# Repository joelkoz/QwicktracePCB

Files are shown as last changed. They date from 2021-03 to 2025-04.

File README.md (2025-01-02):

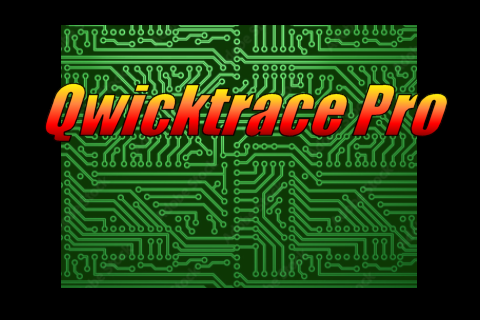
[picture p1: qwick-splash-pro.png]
Qwicktrace Logo


# Qwicktrace Pro PCB
Qwicktrace PCB is the software component of the QwickFab PCB open source desktop circuit board fabrication system.
The system dramatically reduces the time and skill required to make top quality single and double sided circuit 
boards for prototyping and one off use. Using QwickFab PCB, making a PCB is as simple as uploading your Gerber files to 
the Pro controller, selecting the process you wish to use to create the board, and then following the on-screen step
by step instructions. 

# Overview
The QwickFab desktop fabrication system consists of three major hardware components and one optional one:
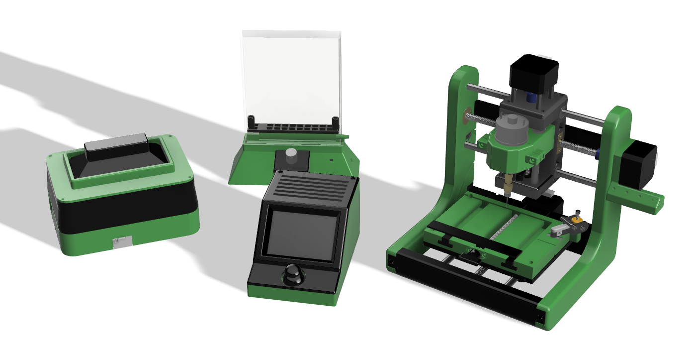
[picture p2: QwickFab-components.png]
Qwicktrace components


1. The Qwicktrace Pro Controller is small control device with touchscreen and joystick powered by a Raspberry Pi 4 and the software
found in this repository. It is comprised of a software stack and UI for controlling the other two hardware components below. The 
Controller can run either of the two other components individually, or together as a complete desktop PCB fabrication system.

2. The Qwicktrace Exposure Table is a small device for quickly exposing photosensitive copper boards to ultraviolet light masked using a process called "Masked Stereolithography" (MSLA). The all new design of this exposure system adds an amber LED "safe light" for illuminating the mask for end user board positioning that is invisible to the photosenstive board.

3. The Qwickmill mini CNC is a small desktop CNC machine designed specifically for working with small printed circuit boards. It can
quickly drill the holes needed by through hole components on boards processed with the Exposure table.  It can also mill an entire PCB on blank copper boards using special ingraving bits. This is handy if your board is simple enough as to not need the better resolution of the exposure table, or if you are on a budget and would prefer not to spend the extra money on photosensitive boards. 
Finally, the Qwickmill can be used to cut board stock down to smaller sizes.

4. The QwickEtch Etching tank is a small container that can be used to quickly etch boards exposed with the Exposure table using
a minimal mount of equipment. While any type of container can be used, the QwickEtch tank has an air pump powered agitator in
in, removing the need for you to manually rock the etching tank.

The software on the Pro Controller (source code found on this repo) handles the more challenging aspects of making a PCB, such as aligning the drilling with the traces made on the exposure table, or positioning the opposite side of a board on a double sided PCB.

While the above hardware components make for a convenient set of tools, many Makers already have existing equipment they'd like
to use in place of a QwickFab component. You are free to mix and match any or all of the components that you wish.  You could
in theory build NONE of the hardware components and simply run the Qwicktrace software on an old laptop or pre-existing 
Raspberry Pi build.  The Qwickmill is built upon the open source standard Grbl controller. If you already own a CNC machines that uses Grbl, you can use that instead. It is easy to create a cable that connects from the Pro Controller to any CNC machine, such a 3018 or 1610. If you are on a budget, you can sometimes source a kit for one of these machines for less money than the individual parts for building the Qwickmill.

# Software features

* Creates PCB trace masks directly from Gerber files in SVG for MSLA exposure and/or in g-code for isolation milling
* Software deskewing of traces and drill holes makes combining MSLA, milling, and/or double sided boards quick and easy.
* Software autoleveling ensures isolation milling traces are cut to perfect depth
* Drill/mill features works with any Grbl compatible CNC controller
* UI designed for small 3.5" touchscreen
* Supports joystick input via ADS1115 for easy jogging of CNC machine and alignment of drill holes
* Turns Raspberry Pi into a remote access server and controller for Grbl CNC machines

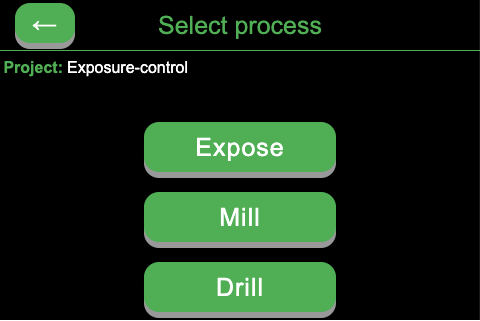
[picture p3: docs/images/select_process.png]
Select process

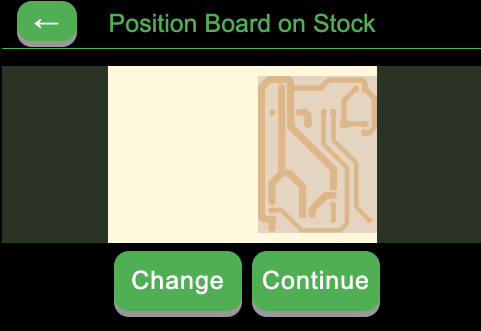
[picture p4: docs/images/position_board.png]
Position board


# DIY construction of a QwickFab system
Qwicktrace components

The Qwickfab Pro system is made from parts printed with your 3D printer as well as easy to obtain off the shelf parts. The
STL files for this project can be found here in this repo in the `hardware/*/stl` directories. A complete bill of materials can be
found in the `docs` directory.

Build instructions with project discussion is located on the project's [Hackaday Project Page](https://hackaday.io/project/182645-qwickfab-pcb)

To install the software on the Raspberry Pi, see the file `Setting up Raspberry Pi`, also in `docs`

# Development

The Qwicktrace user interface on the Pro Controller is a touchscreen app written in NodeJS/Javascript and built with the
Electron framework.  This UI is layered on top of a software stack comprised of many great open source software packages. These include:

1. [Tracespace](https://github.com/tracespace) Gerber processing library for Javascript
2. [pcb2gcode](https://github.com/pcb2gcode/pcb2gcode) Gerber to GCode utility for milling isolation traces
3. [CNCjs](https://github.com/cncjs/cncjs) Web interface and Grbl server for CNC machine control
4. [EventEmitter2](https://github.com/EventEmitter2/EventEmitter2) Advanced event handling for NodeJS

For additional technical information on the Qwicktrace software architecture, see the `docs` directory

---
### Do you find my work useful?

<a href="https://www.buymeacoffee.com/joelkoz" target="_blank">Buy Me A Coffee</a>
---

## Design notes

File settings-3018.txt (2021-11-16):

$0=10 (Step pulse time, microseconds)
$1=25 (Step idle delay, milliseconds)
$2=0 (Step pulse invert, mask)
$3=6 (Step direction invert, mask)
$4=0 (Invert step enable pin, boolean)
$5=0 (Invert limit pins, boolean)
$6=0 (Invert probe pin, boolean)
$10=1 (Status report options, mask)
$11=0.020 (Junction deviation, millimeters)
$12=0.002 (Arc tolerance, millimeters)
$13=0 (Report in inches, boolean)
$20=0 (Soft limits enable, boolean)
$21=1 (Hard limits enable, boolean)
$22=1 (Homing cycle enable, boolean)
$23=0 (Homing direction invert, mask)
$24=25.000 (Homing locate feed rate, mm/min)
$25=1000.000 (Homing search seek rate, mm/min)
$26=250 (Homing switch debounce delay, milliseconds)
$27=1.000 (Homing switch pull-off distance, millimeters)
$30=20000 (Maximum spindle speed, RPM)
$31=0 (Minimum spindle speed, RPM)
$32=0 (Laser-mode enable, boolean)
$100=800.000 (X-axis travel resolution, step/mm)
$101=800.000 (Y-axis travel resolution, step/mm)
$102=800.000 (Z-axis travel resolution, step/mm)
$110=1000.000 (X-axis maximum rate, mm/min)
$111=1000.000 (Y-axis maximum rate, mm/min)
$112=600.000 (Z-axis maximum rate, mm/min)
$120=50.000 (X-axis acceleration, mm/sec^2)
$121=50.000 (Y-axis acceleration, mm/sec^2)
$122=50.000 (Z-axis acceleration, mm/sec^2)
$130=289.000 (X-axis maximum travel, millimeters)
$131=175.000 (Y-axis maximum travel, millimeters)
$132=37.85 (Z-axis maximum travel, millimeters)

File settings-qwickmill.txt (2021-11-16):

$0=10 (Step pulse time, microseconds)
$1=25 (Step idle delay, milliseconds)
$2=0 (Step pulse invert, mask)
$3=2 (Step direction invert, mask)
$4=0 (Invert step enable pin, boolean)
$5=0 (Invert limit pins, boolean)
$6=0 (Invert probe pin, boolean)
$10=1 (Status report options, mask)
$11=0.010 (Junction deviation, millimeters)
$12=0.002 (Arc tolerance, millimeters)
$13=0 (Report in inches, boolean)
$20=0 (Soft limits enable, boolean)
$21=1 (Hard limits enable, boolean)
$22=1 (Homing cycle enable, boolean)
$23=0 (Homing direction invert, mask)
$24=25.000 (Homing locate feed rate, mm/min)
$25=1000.000 (Homing search seek rate, mm/min)
$26=250 (Homing switch debounce delay, milliseconds)
$27=1.000 (Homing switch pull-off distance, millimeters)
$30=26666 (Maximum spindle speed, RPM)
$31=0 (Minimum spindle speed, RPM)
$32=0 (Laser-mode enable, boolean)
$100=400.000 (X-axis travel resolution, step/mm)
$101=400.000 (Y-axis travel resolution, step/mm)
$102=400.000 (Z-axis travel resolution, step/mm)
$110=1000.000 (X-axis maximum rate, mm/min)
$111=1000.000 (Y-axis maximum rate, mm/min)
$112=600.000 (Z-axis maximum rate, mm/min)
$120=30.000 (X-axis acceleration, mm/sec^2)
$121=30.000 (Y-axis acceleration, mm/sec^2)
$122=30.000 (Z-axis acceleration, mm/sec^2)
$130=200.000 (X-axis maximum travel, millimeters)
$131=200.000 (Y-axis maximum travel, millimeters)
$132=200.000 (Z-axis maximum travel, millimeters)

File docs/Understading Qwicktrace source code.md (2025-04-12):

General functionality of QwicktracePCB app:
========

Workflow
------
- User creates a collection of Gerber files for each layer of a PCB, and a DRL file for hole definitions using
  their EDA (KiCad, Eagle, etc.). 
  - Be sure that the origin of your board is at the lower left hand corner
  - Files that represent the top and/or bottom copper layer, along with the DRL file should be bundled into a single .zip file.
  - The .ZIP file name is used as the project name inside of QwicktracePCB. 
  - The .ZIP file name should NOT contain any spaces
- Upload the .ZIP file to the app using `http://pcb.local:8080`
- Use the UI of QwicetracePCB to fabricate the board

Troubleshooting
-------
- Just before milling or exposure starts, the gerber and drill files actually used will be stored in `/temp`
- You can examine the .GBR or .DRL files with the `gerbv` utility to make sure they represent your board.
- Gcode used for milling and drilling are stored in `/temp` with file extensions `.nc`
- You can manually updload the `.nc` files and manually control the milling process by accessing CNCjs directly
  at `http://pcb.local:8000`
- Since the CNC mill is controlled via the CNCjs layer, you can actually run the QuicktracePCB UI and control code directly 
  from a PC or Mac and observe the logs.
  - Edit the `config.json` file and change the `cnc.server.host` and the `pigpio.host` entries to be the IP of
    the Qwicktrace controller. Do NOT use the DNS name "pcb.local", as the code may not properly resolve those names
  - Run the Qwicktrace UI from the desktop by changing the current directory to the `QwicktracePCB` root and
    executing `npm run start` from the terminal.

- Regenerate gcode for traces with
```
pcb2gcode --front ./temp/mirror-bottom.gbr --front-output ./temp/bottom-mill.nc
```

Project outline
-----
- Source code is in `app` directory
- ZIP files of gerber/drill bunders are stored in `pcb-files`
- Definitions for raw material types and stock of those materials are in `profiles`
  - A "material" defines a general type of raw material (copper board, photosenstive board, etc)
  - A "stock" is a raw material cut to a particular size
- Configuration file for app is `config.json`. It defines the fabrication tools available and their configuration
  - use `config-3018.json` if milling pcb with a standard 3018 CNC Mill
  - use `config-pi-pro.json` if milling and/or exposing with a Qwickpro build
- If pcb trace isolation is done using a mill, then `pcb2gcode` app is used to translate gerber into gcode. The
  file `millproject` defines the parameters passed in to this CLI app. 

Source overview
------
- App is a desktop app that uses Electron to provide a runtime environment
- App is structured as a typical client/server app, even though it is bundled inside Electron
- "Server" code is the only code that can talk to/control hardware (hard drive, mill, exposure table)
- "Client" code is a html+javascript web app
- "Server" code is located in `main` directory
- "Client" code is located in `render` directory
- The two layers communicate with each other with a publish/subscribe model using message queue management provided
  by `MainMQ.js` and `RenderMQ.js`
- There is a "remote procedure call" mechanism built on top of `MainMQ.js` and `RenderMQ.js` named `RPCServer.js` and 
  `RPCClient.js` respectively
- The main application logic and program flow is handled in the "Client".  The "Server" provides supporting services
  and does the actual work.

Server side code
------------
- Code found in `app/main`
- `main.js` is the server side entrypoint with startup code. It creates the Electron browser window for the UI,
   loads the UI (via `UILoader.js`), then sets up message handers the client may call
- `ProjectLoader.js` is a singleton that manages a collection of all of the PCB projects stored in `pcb-files.js`
  - Each entry is an instance of `pcb/PCBProject.js`
  - Each project is sent to the UI for user selection
  - Has a method named `prepareForWork()` that prepares all of the files necessary to be processed
- `ProfileLoader.js` is a singleton that reads the definitions of all of the material and stock profiles and sends
   them to the ui
- A series of "Controller" objects control the various hardware sub systems. Each are a collection of work methods
  that do the work of fabrication.  Many can be called directly by the client via the RPC mechanism (look for 
  `this.rpcAPI()` to see what methods are exposed as callable via RPC).
  - `CNCController.js` handles milling and drilling
  - `JoystickController.js` handles the system joystick
  - `UVController.js` handles the exposure table
- A low level CNC control object that interfaces with CNCjs can be found in `cnc/CNC.js`
- If milling a PCB's traces using trace isolation, Gerber to GCode translation is handled by the `pcb2gcode`
  command line tool. `cnc/GcodeUtils.js` is the server's interface to this tool which invokes `pcb2gcode`

Client side code
----------------
- Code found in `app/render`
- UI is composed of a series of individual "pages" that the user moves through.
  - Pages are located in `app/render/ui`
  - A page definition contains CSS and a root `&lt;DIV&gt;`. The `DIV` in turn can contain
    whatever HTML needs to be displayed
  - Page flow is controlled by `UIController.js`
  - A "wizard" is a collection of pages that leads a user step by step thru a particular
    function. Wizards are created by definition a JSON structure that contains the name
    of the wizard and a series of "steps". Each step composed of a string id that identifies the
    step, text instructions to give the user, the buttons to present to the user and the "handler"
    code to execute when that button is pressed, as well as code to execute then the page is first
    activated, and when it is deactivated.
- A series of "Controller" objects represent by each functional subsystem. They define both the
  UI of that subsystem, as well as handle the communication with the hardware controllers on the "server"
  via RPC. Generally, a feature will define a wizard to handle the feature, then will delegate to the
  UIController to execute the wizard.
  - `UIController.js` Top level UI that delegates to the various features and sub-systems. Also executes
     the "wizard" UI feature.
  - `DrillController.js` Feature allows thru holes to be drilled in a PCB
  - `MillController.js` Feature that allows a PCB to be fabricated using a CNC to do trace isolation
  - `ExposeController.js` Featuure that allows a PCB to be fabtricated using UV sensitive PCB boards
  - `PositionController.js` A sub-system that allows the user to position the traces on stock of a particular size
  - `SettingsController.js` Feature allows user to modify system configuration, as well as perform utility functions
    like cutting stock

PCB milling
=====================
- Gerber and DRL files are converted to GCode for milling by:
- `app/main/ProjectLoader.js` methods `prepareForWork()`, `getFinalGerber()`, and `getWorkAsGcode()`
- `prepareForWork()` and `getFinalGerber()` takes the project files and transforms them, positioning
  them on the stock, and mirroring the traces (if milling the bottom of the board). Transformed
  gerber files are placed in the `/temp` directory
- `getWorkAsGcode()` translates those files in Gcode via `app/main/cnc/GcodeUtils.js`, and stores the
  results in the `/temp` dir as `.nc` files.
- `GcodeUtils.js` delegates to `pcb2gcode` to do the actual translation, Parameters to `pcb2code` are stored
  in the `millproject` file.  
- To actually mill the traces of a PCB, `app/render/MillController.js` makes the rpc call `cnc.millPCB` which
  is executed by `app/main/CNCController.js` in the `millPCB()` method. That in turn makes a series of calls
  to `app/cnc/CNC.js` to control each step of the milling process.

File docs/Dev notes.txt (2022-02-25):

RaspPi splash screen is here
/usr/share/plymouth/themes/pix/splash.png

Thus, plymouth is already installed.

Ideas:
Use input pin to specify if probe arm is connected or not.  Use status report from grbl to see if 
clip is connected or not.  Thus:
1. Ground clip screw
2. Connect pin from pi to arm strip and read to see if arm is in place

Remove M3 from pcb2gcode output, and use our own ramp up code to turn on spindle.

Add a red "emergency stop" button to bit holder and connect it to Grbl alarm pin

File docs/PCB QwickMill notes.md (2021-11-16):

# Qwicktrace PCB Pro Notes

This file contains general notes I made as I was developing the mill and its software.

## Tips and tricks for milling

### Critical tips
* Bit must be TIGHT. Otherwise, vibration causes slip, which ruins z-height.
* X and Y bearings must be secure. Y bearing slipped out, ruining z-height during mill

### Important tips
* When cutting, there is some wobble in the bit, so make sure to give a little extra room when 
  locating position
* 1mm drill bit is fairly large.  0.9mm is better. 0.8mm is tight fit, but some components may not fit
* 30 degree VBit made a much smoother cut than then 5/32" end mill

### Helpful hints
* Place a sheet of tin foil over milled PCB to be able to zprobe or autolevel it
* Scouring pad is great to clean up loose copper bits after milling

## Controller display
Connect hdmi cable for the Sharp display used in the exposure table to HDMI:0

External Display (i.e. any local display) would be HDMI:1

Customizing splash screen:
https://shop.sb-components.co.uk/blogs/posts/customising-splash-screen-on-your-raspberry-pi

## Important GCodes
```
G21 = Units in mm
G0 = Rapid position
G1 = Linear interpolation (position at current feedrate defined by previous "F")
```

Spindle on:
```
M03 S20000.0
```

Spindle off:
```
M05
```
```
G91 = Relative coordinate mode
G90 = Absolute coordinate mode
```
Doing a single probe (feed 20mm per minute, up to 14mm down from current point):
```
G91
G38.2 Z-14 F20
G90
```

## Using gerbv 

gerbv in GUI mode (just issue gerbv) allows one to examine gerber files
and drill files visually (e.g. look at intermediate files)

Using gerbv to manipulate gerber files:
```
// Rotate gerber clockwise 90 degrees:
gerbv -u mm -x rs274x -T "0x${width}r270" -o "${outFile}" "${inFile}"
```

```
// Rotate gerber counter clockwise 90 degrees:
gerbv -u mm -x rs274x -T "${height}x0r90" -o "${outFile}" "${inFile}"
```

## Using pcb2gcode to generate gcode for mill:

Create a file named "millproject" to save parameters
(vs. issuing on cli):
```
## Default options passed to pcb2gcode when generating
metric=true
metricoutput=true

# For use with grbl
software=custom
nog64=true
nog81=true

# Engraving traces
zwork=-0.25
zsafe=5
mill-feed=40
mill-speed=8500
offset=0.5

# Drilling holes
zdrill=-2.1
zchange=1.0
drill-feed=75
drill-speed=6000
onedrill=true
```
Since we manipulate gerber files internally (e.g. bottom files are
mirrored then saved to intermediate gerber file), always specify
"front" for pcb2gcode so it won't mirror a second time.

Generate gcode for copper:
```
pcb2gcode --front inputFileName.gbr --front-output outputFileName.nc
```

Generate gcode for drilling:
```
pcb2gcode --drill-side front --drill inputFileName.drl --drill-output outputFileName.nc
```

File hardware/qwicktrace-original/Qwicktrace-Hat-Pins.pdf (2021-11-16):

VCC + LED | 3.3v | 1 | 2 | 5v
I2C SDA | GPIO 2/SDA | 2 | 4 | 5v
I2C SCL | GPIO 3/SCL | 5 | 6 | GND
| GPIO 4 (GPCLK0) | 7 | 8 | GPIO 14 (TX) | UV LED BED
| GND | 9 | 10 | GPIO 15 (RX)
CS | GPIO 17 | 11 | 12 | GPIO 18 (PCM_CLK)
RESET | GPIO27 | 13 | 14 | GND
DC | GPIO 22 | 15 | 16 | GPIO 23
| 3.3v | 17 | 18 | GPIO 24
MOSI + T_DIN | GPIO 10 (MOSI) | 19 | 20 | GND
MISO + T_DO | GPIO 9 (MISO) | 21 | 22 | GPIO 25
SCK + T_CLK | GPIO 11 (SCLK) | 23 | 24 | GPIO 8 (CE0)
| GND | 25 | 26 | GPIO 7 (CE1)
| GPIO 0 (ID_SD) | 27 | 28 | GPIO 1 (ID_SC)
T_CS | GPIO 5 | 29 | 30 | GND
T_IRQ | GPIO 6 | 31 | 32 | GPIO 12 (PWM0)
| GPIO 13 (PWM1) | 33 | 34 | GND
CNC ZProbe | GPIO 19 (PCM_FS) | 35 | 36 | GPIO 16 | BUZZER
CNC LASER PTR | GPIO 26 | 37 | 38 | GPIO 20 (PCM_DIN)
GND | GND | 39 | 40 | GPIO 21 (PCM_DOUT)

1

Pi Hat to TFT wiring

16 Ribbon wire color | Multi/Shared 40 Pin | GPIO num | 40 Pin Num | 40 pin Col 1 row num | IDC 16P pin number | TFT connection | Make Longer
Brown | * | 3v3 | 1 | 1 | 1 | VCC
Red | * | 3v3 | 1 | 1 | 2 | LED | **
Orange | | GND | 9 | 5 | 3 | GND
Yellow | | GPIO17 | 11 | 6 | 4 | CS
Green | | Unused | | | 5
Blue | | GPIO27 | 13 | 7 | 6 | DC
Purple | | Unused | | | 7
Grey | | GPIO22 | 15 | 8 | 8 | RESET
White | * | MOSI/GPIO10 | 19 | 10 | 9 | T_DIN | **
Black | * | MOSI/GPIO10 | 19 | 10 | 10 | SDI(MOSI)
Brown | * | MISO/GPIO9 | 21 | 11 | 11 | SDO(MISO)
Red | * | MISO/GPIO9 | 21 | 11 | 12 | T_DO
Orange | * | SLCK/GPIO11 | 23 | 12 | 13 | SCK
Yellow | * | SLCK/GPIO11 | 23 | 12 | 14 | T_CLK
Green | | GPIO6 | 31 | 16 | 15 | T_CS
Blue | | GPIO5 | 29 | 15 | 16 | T_IRQ

1

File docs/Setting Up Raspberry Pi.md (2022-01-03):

# Setting up Raspberry Pi
This is a very rough list of things needed to do to setup the Raspberry Pi and install this QwicktracePCB controller software on it

1. Download and use "Raspberry Pi Imager" to flash an SD card from your desktop computer. Use recommended 32 bit OS on main menu. You need the OS 'with Desktop Software'.

2. Before installing the SD card in the Pi, create the file `ssh` in the root directory of the SD card. This can be done on a Mac by using Terminal, then typing `echo >/Volumes/boot/ssh`

3. On the same SD card, create the file `wpa_supplicant.conf` with the following contents:
```
country=US
ctrl_interface=DIR=/var/run/wpa_supplicant GROUP=netdev
update_config=1

network={
  ssid="NETWORK-NAME"
  psk="NETWORK-PASSWORD"
}
```

4. Replace the contents of the file `config.txt` on the SD card with the file found in the `pi-config/boot` directory of this project. It can be downloaded to your desktop computer using [this link](https://raw.githubusercontent.com/joelkoz/QwicktracePCB/main/pi-config/boot/config.txt).

5. Put the SD card in the Pi and boot. 

6. Use `ssh` to connect to the Pi from your desktop. It should be available on your network as `raspberrypi.local`.  Thus, `ssh pi@raspberrypi.local` should connect you. The default password is `raspberry`.

7. Change the password using the `passwd` command.

8. Install the software for whichever screen you are using. For the new "Qwicktrace Pro" controller, follow
the directions found in the `U6111-UC640.pdf` file in the `docs` directory of this repo.

8. Update all software using these commands:
```
sudo apt update
sudo apt full-upgrade
```

9. Configure the system with raspi-config:
```
sudo raspi-config

   *  Use the System Options to specify "Boot to command line" (in case something weird goes wrong)
   
   *  Change the host name to `pcb`
```

10. Install required software and utilities:
```
sudo apt-get update
sudo apt-get install nodejs
sudo apt-get install npm
sudo apt-get install fbi
```

11. From your home Pi directory, install the software from this project:
```
cd ~
git clone https://github.com/joelkoz/QwicktracePCB
cd QwicktracePCB
npm install
```

12. Install the X11 multihead configuration:
```
sudo cp /home/pi/QwicktracePCB/pi-config/x11/99-multihead.conf /usr/share/X11/xorg.conf.d
```

13. Enable the `pigpiod` daemon to give the software access to the GPIO pins:
```
sudo nano /lib/systemd/system/pigpiod.service
change line to:
ExecStart=/usr/bin/pigpiod -n 127.0.0.1 -p 8888

save file

sudo systemctl daemon-reload
sudo systemctl enable pigpiod
sudo service pigpiod start
```

NOTE: If you want to be able to access pigpiod remotely (for remote development, for example),
add additional allowed IP addresses to the `ExecStart` command above:
```
ExecStart=/usr/bin/pigpiod -n 127.0.0.1 -n 192.168.0.152 -p 8888
```

15. Disable Bluetooth related services:
```
sudo systemctl disable hciuart.service
sudo systemctl disable bluetooth.service
```

15. Disable other unneeded services
```
sudo systemctl disable cups.service cups.socket cups.path
sudo systemctl disable cups-browsed.service
```

15. Reboot the Pi:
```
sudo reboot
```

16. Connect back to the Pi via ssh. The DNS name of the machine should now be `pcb.local`, so use `ssh pi@pcb.local`

17. Test to see if the small SPI screen is working. An image on the small screen should appear after:
```
sudo fbi -T 7 -d /dev/fb2 -noverbose /home/pi/QwicktracePCB/qwick-splash-pro.png
```

18. Configure desktop to run Qwicktrace exclusively:
```
sudo cp /etc/xdg/lxsession/LXDE-pi/autostart /etc/xdg/lxsession/LXDE-pi/autostart-desktop

sudo cp /home/pi/QwicktracePCB/pi-config/lxde/autostart-app /etc/xdg/lxsession/LXDE-pi

sudo cp /etc/xdg/lxsession/LXDE-pi/autostart-app /etc/xdg/lxsession/LXDE-pi/autostart
```

19. Disable cursor on touchscreen:
```
sudo nano /etc/lightdm/lightdm.conf

Find the [Seat*] section, uncomment the "#server-command=" line, and make it:

xserver-command=X -nocursor
```

20. Install the splashscreen services
```
sudo cp /home/pi/QwicktracePCB/pi-config/etc/systemd/system/* /etc/systemd/system
sudo systemctl enable splashscreen.service
```

20. Install CNC control services (if using QwickMill or other CNC machine):
The following steps come from the official [CNCjs Pi install pages](https://cnc.js.org/docs/rpi-setup-guide/). Note
that to avoid problems with `serialport` library, cncjs is **NOT** installed as `root` with `sudo`
```
sudo apt-get update
sudo apt-get upgrade -y
sudo apt-get dist-upgrade -y
sudo apt-get install -y build-essential git
sudo apt-get install htop iotop nmon lsof screen -y

npm install -g cncjs@latest
sudo npm install -g pm2
pm2 startup
sudo env PATH=$PATH:/usr/bin /usr/local/bin/pm2 startup systemd -u pi --hp /home/pi
pm2 start $(which cncjs) -- --port 8000
pm2 save
pm2 list
```

Installing Autoleveling plugin for CNCjs:
```
cd /usr/local
sudo mkdir cncjs-kt-ext
sudo chown pi cncjs-kt-ext/
git clone https://github.com/joelkoz/cncjs-kt-ext.git
cd cncjs-kt-ext
npm install
nano pm2.config.js
```

Contents of pm2.config.js:
```
module.exports = {
  apps : [
      {
        name: "autolevel",
        script: ".",
        args: "--port /dev/ttyUSB0"
      }
  ]
}
```

Final commands to autoload Autolevel plugin:
```
pm2 start pm2.config.js
pm2 save
```

Command to show the splashscreen again, since loading CNCjs utility takes about 20+ seconds...
```
sudo systemctl enable splashscreen2.service
```

20. Start the desktop system and make sure everything is working:
```
sudo service display-manager start
```

21. If all is well, re-enable "Boot to desktop, auto logged in as 'pi'" using raspi-config:
```
sudo raspi-config
```

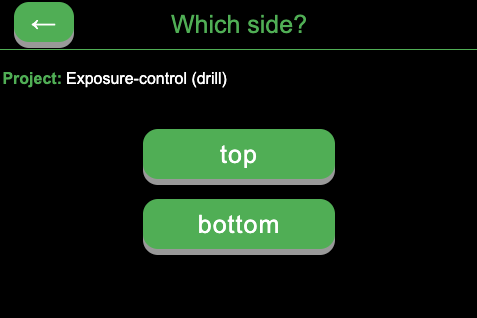
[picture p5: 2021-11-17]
docs/images/select_side.png

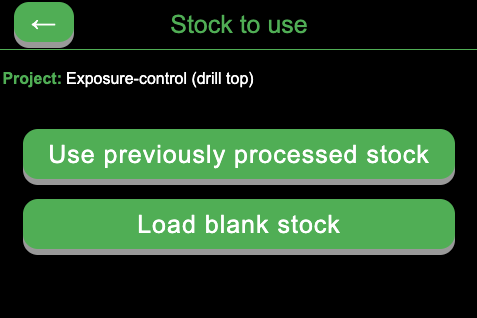
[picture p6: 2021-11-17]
docs/images/select_stock.png

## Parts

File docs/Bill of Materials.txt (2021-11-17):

Here are links to the parts needed to build a QwickFab system:

Pro Controller:
https://www.amazon.com/ideas/amzn1.account.AGOOJYS2GJN5RQEZXXSSGWMG2SAA/1ZQ695RBORSNX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

QwickMill CNC:
https://www.amazon.com/ideas/amzn1.account.AGOOJYS2GJN5RQEZXXSSGWMG2SAA/2YNZ9RROMNI52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

Qwicktrace exposure table:
https://www.amazon.com/ideas/amzn1.account.AGOOJYS2GJN5RQEZXXSSGWMG2SAA/3AY03VCI9K1BM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

https://www.banggood.com/Sparkmaker-UV-Backlight-Lamp-Board-400-410nm-24W-for-UV-Resin-3D-Printer-p-1493455.html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

QwickEtch tank:
https://www.amazon.com/ideas/amzn1.account.AGOOJYS2GJN5RQEZXXSSGWMG2SAA/317JX247P1HNQ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

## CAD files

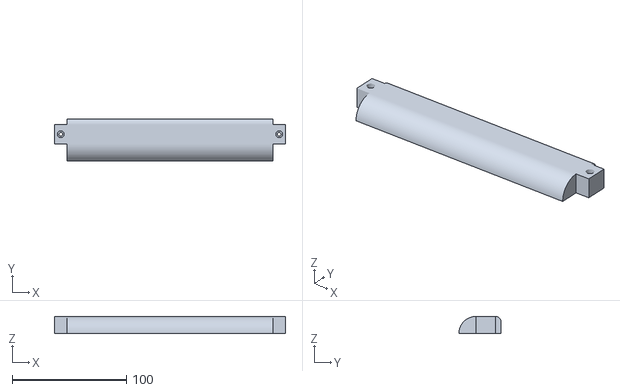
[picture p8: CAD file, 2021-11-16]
hardware/cnc/stl/BaseFront.stl
202.0 x 37.0 x 15.0

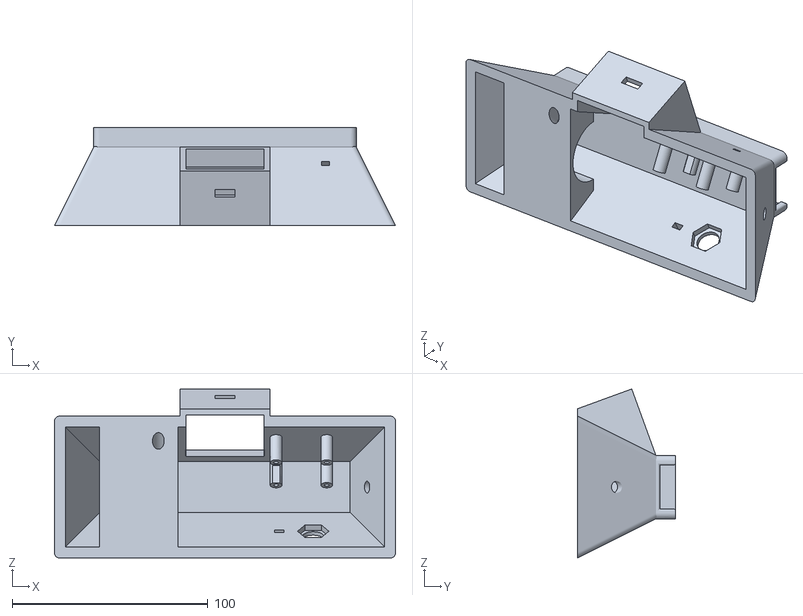
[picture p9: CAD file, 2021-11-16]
hardware/etch-tank/stl/Base.stl
174.0 x 50.0 x 86.2

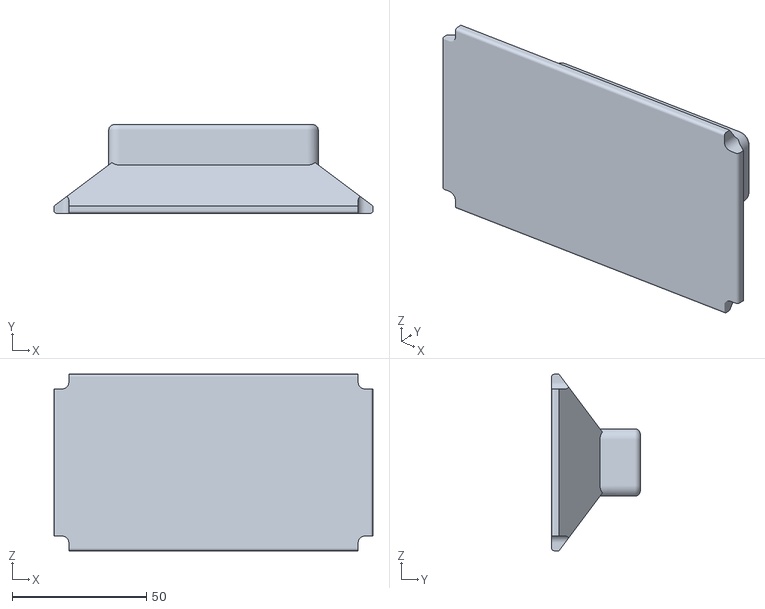
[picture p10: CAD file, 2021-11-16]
hardware/exposure-table/stl/Lid.stl
118.7 x 33.0 x 65.7

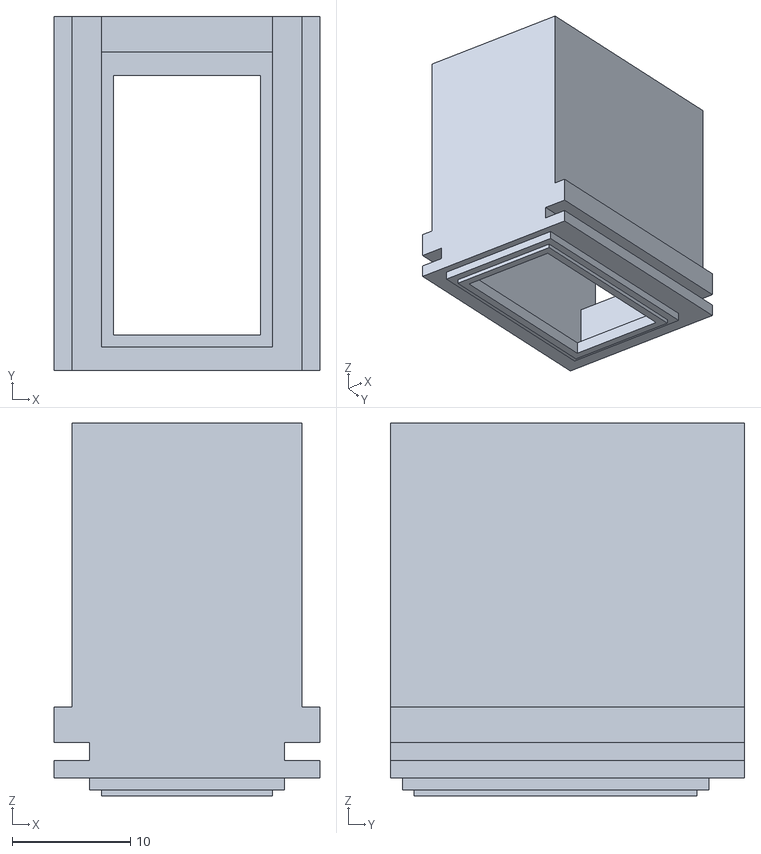
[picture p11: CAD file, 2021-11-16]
hardware/pro-controller/stl/HDMI-mount.stl
22.4 x 29.9 x 31.5

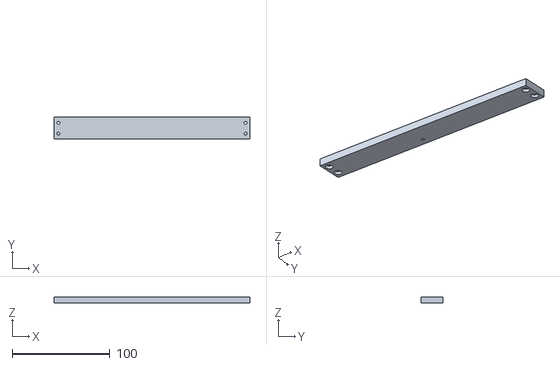
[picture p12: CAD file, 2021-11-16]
hardware/cnc/stl/ControllerMount.stl
200.0 x 22.5 x 6.10

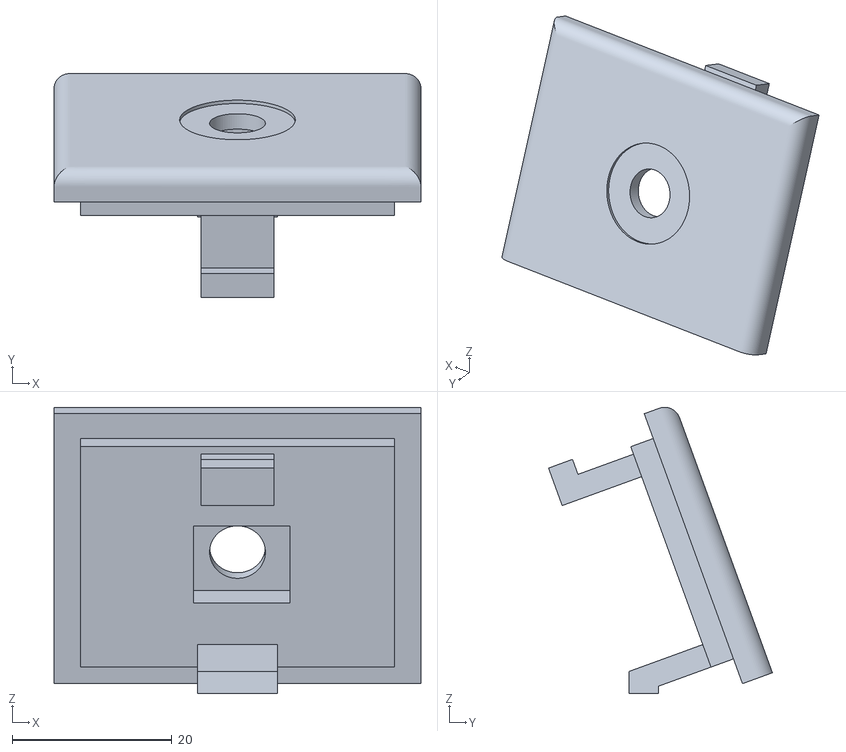
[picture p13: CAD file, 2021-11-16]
hardware/etch-tank/stl/ControlLid.stl
46.0 x 28.1 x 35.9

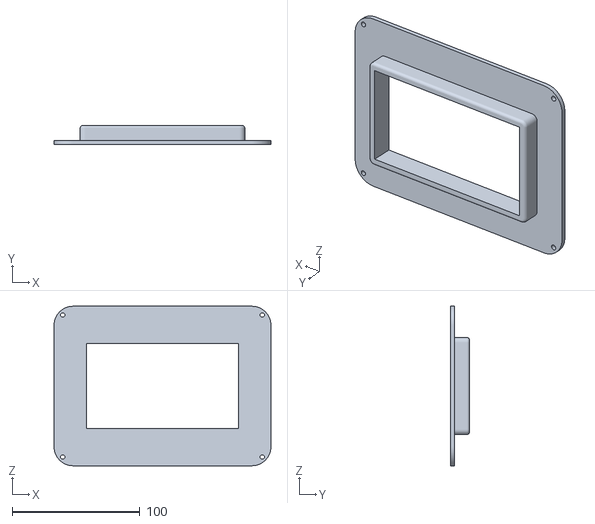
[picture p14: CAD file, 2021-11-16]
hardware/exposure-table/stl/AlignmentFrame.stl
170.0 x 15.0 x 125.0

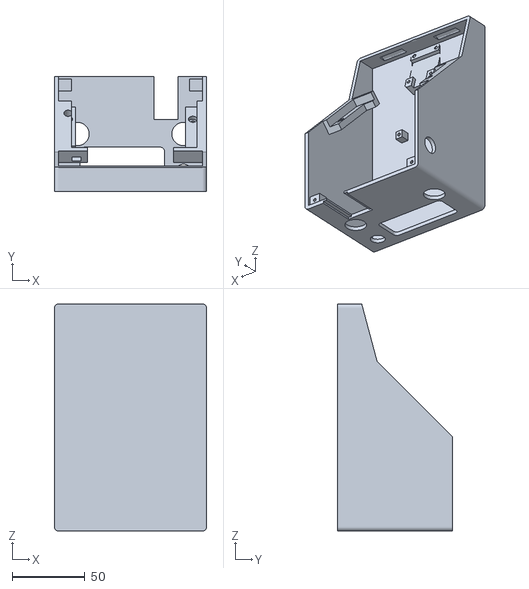
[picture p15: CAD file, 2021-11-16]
hardware/pro-controller/stl/ControllerBase.stl
105.0 x 79.5 x 156.3

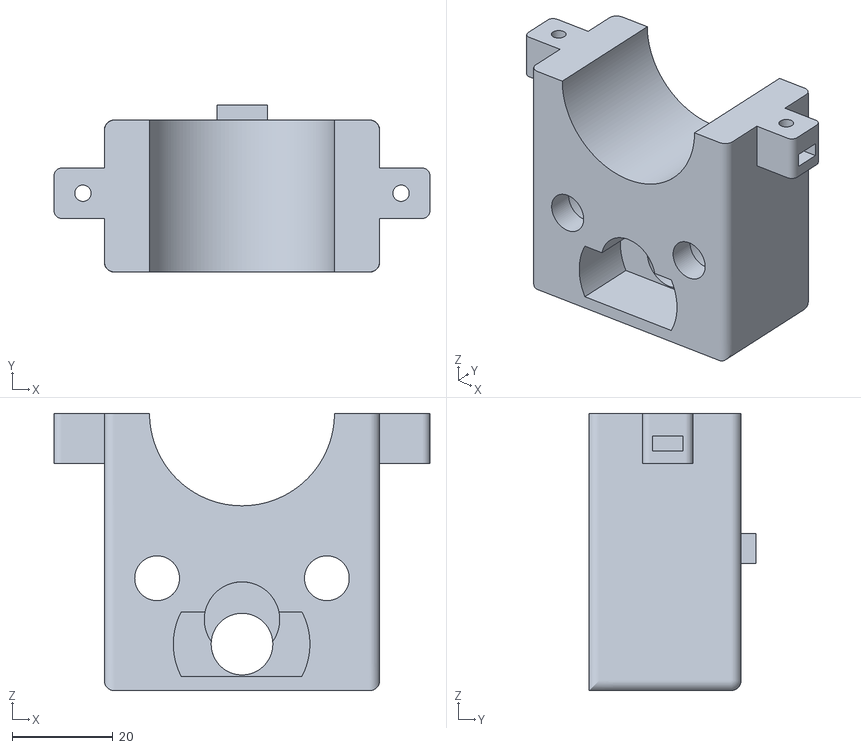
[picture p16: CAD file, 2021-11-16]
hardware/cnc/stl/SpindleMountBase.stl
74.8 x 33.2 x 55.1

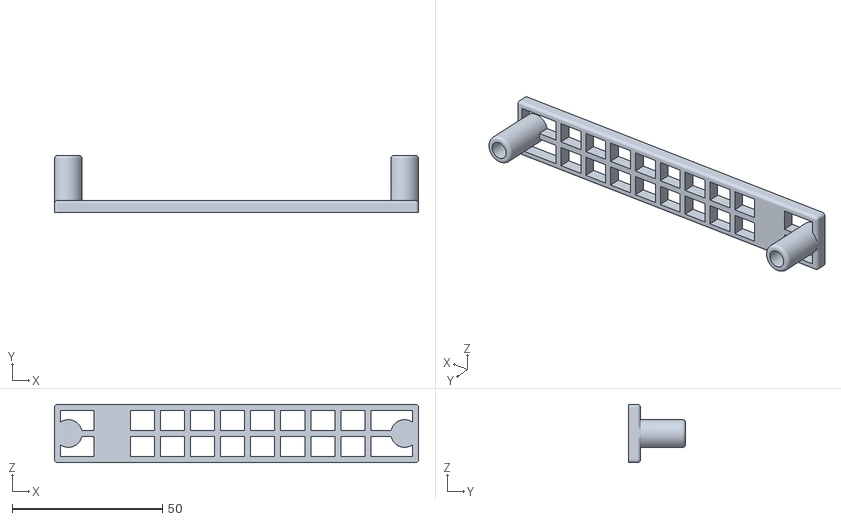
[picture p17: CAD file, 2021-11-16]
hardware/etch-tank/stl/Basket.stl
121.0 x 19.0 x 19.4

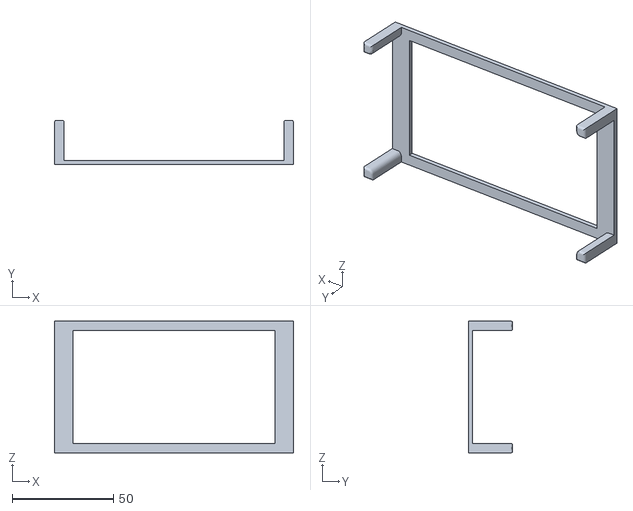
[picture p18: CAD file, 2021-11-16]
hardware/exposure-table/stl/BasicTray.stl
118.3 x 22.0 x 65.3

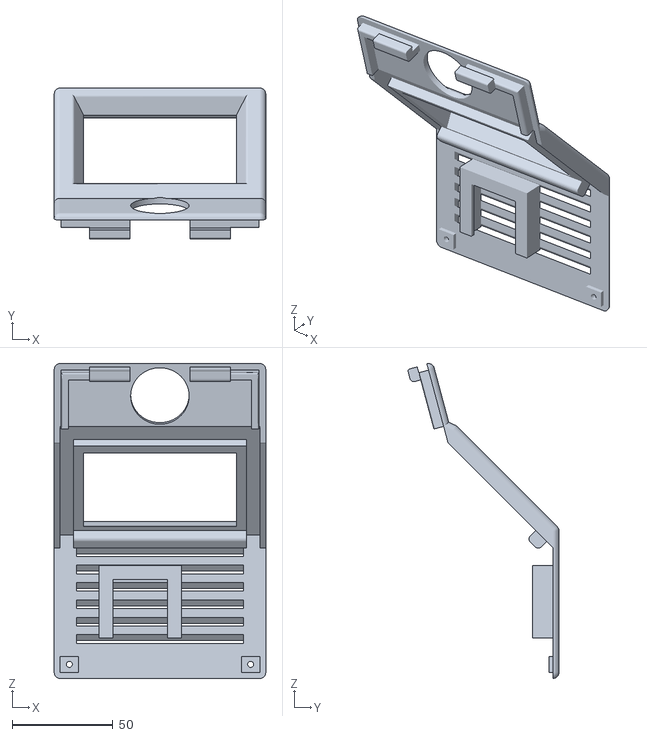
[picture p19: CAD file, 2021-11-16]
hardware/pro-controller/stl/ControllerLid.stl
105.0 x 75.0 x 156.3

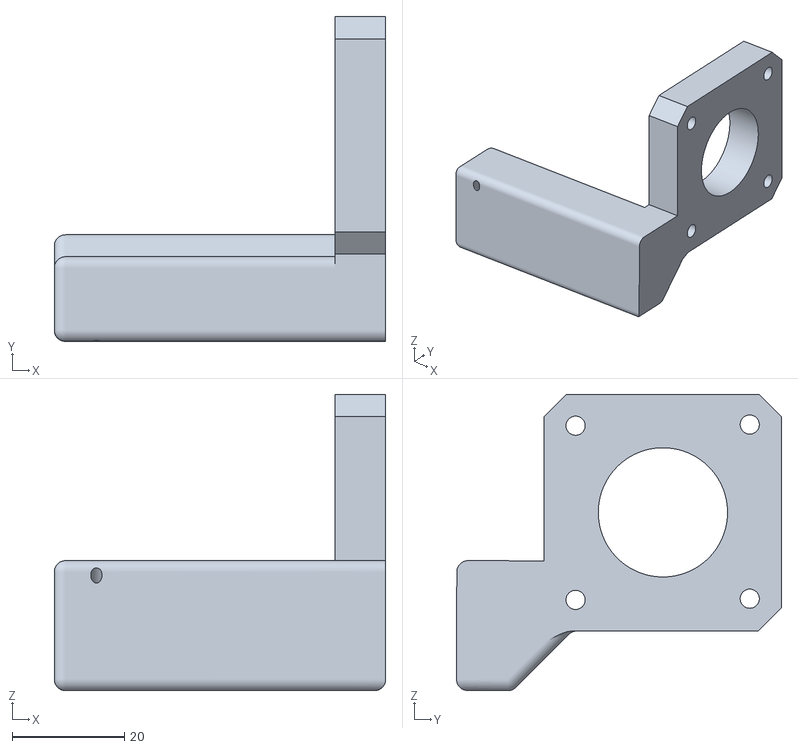
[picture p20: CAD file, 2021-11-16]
hardware/cnc/stl/XStepperSpacer.stl
59.0 x 57.8 x 52.7

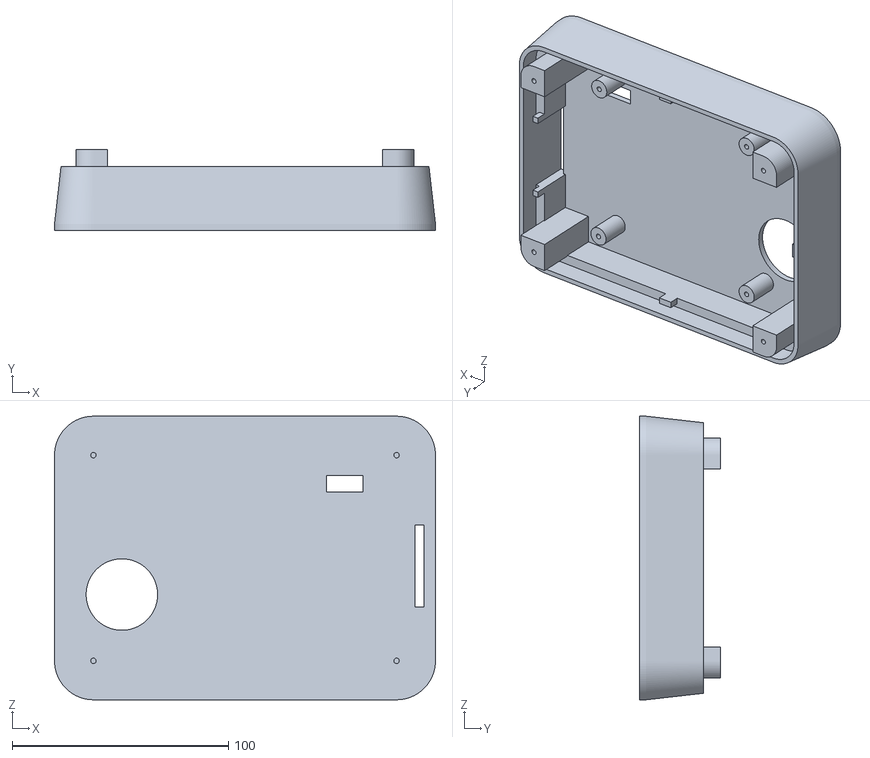
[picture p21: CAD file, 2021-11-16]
hardware/exposure-table/stl/LED layer.stl
176.0 x 37.3 x 131.0

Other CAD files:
hardware/cnc/stl/PCBBedBase.stl
hardware/exposure-table/stl/SafeBulbSocket.stl
hardware/cnc/stl/ZPogoMount.stl
hardware/exposure-table/stl/ControlBoardBrace.stl
hardware/cnc/stl/BaseBack.stl
hardware/cnc/stl/BaseLeft.stl
hardware/cnc/stl/BaseRight.stl
hardware/cnc/stl/SideFence.stl
hardware/cnc/stl/SpindleMountBracket.stl
hardware/cnc/stl/ViceHandle.stl
hardware/cnc/stl/ViceScrewCover.stl
hardware/cnc/stl/XMount.stl
hardware/cnc/stl/XMountCap.stl
hardware/cnc/stl/YBedAllInOne.stl
hardware/cnc/stl/ZPogoMountBase.stl
hardware/cnc/stl/ZPogoMountCap.stl
hardware/exposure-table/stl/CableDoor.stl
hardware/exposure-table/stl/Footer.stl
hardware/exposure-table/stl/ScreenBase.stl

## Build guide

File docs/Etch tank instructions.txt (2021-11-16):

Materials:
5" x 7" x 2mm (127 mm x 177.8 mm x 2 mm) cast acrylic sheets

Needed:
Front and Back:
127 mm x 153.625 mm

Bottom:
127mm x 21mm

Left and Right Sides:
21 mm x 151.625 mm

Mill sheets as follows:

TIP: Mark 21 mm from right as WorkX zero. All 21 mm cuts will then match.

1. Mill 2 sheets, cutting 21 mm off long side with 3.175 bit yields:

a. 2 @ 127 mm x 153.625 mm
b. 2 @ 127 mm x 21 mm

"a" is front and back.  One of "b" is "bottom". Second "b" is scrap

2. Mill 1 sheet, cutting 23 mm off long side with 3.175 bit yields:

a. 1 @ 127 mm x 151.625
b. 1 @ 127 mm x 23 mm 

"a" is used next. "b" is scrap

TIP: Rotate 2a so 151.625 is on Y axis. Use WorkX zero from 1 to cut
width as 21 mm

3. Mill 2a by cutting off two strips, 21 mm width each with 3.175 bit yields:

a. 2 @ 21 mm x 151.625
b. 1 @ 78.65 mm x 151.625

"a" is left and right. "b" is scrap

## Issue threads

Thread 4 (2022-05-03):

Documentation Improvements

nebulorum, 2022-05-03:
Congratulations on a great idea. I was looking for experiences on using LCD for etching and solder masking. This is a validation that it makes sense.  Just going through the project I found some minor documentations issues:

* The BOM has link for the LCD no longer works, it would be nice to have the spec of the item.
* It's not clear how to build the project or run it as a developer.

I would also like to test the software before building something like this. I also wonder if I couldn't run the software on my PC and drive the display from it.

Anyway great work.

nebulorum, 2022-05-04:
Was really curious and decided to clone and try to run. I managed to get is started without `config-dev.json` and the CNC disabled. I could upload files. However the Electron only shows a black screen. When I reload the Electron page I do see the UI flash before being covered by a black window.

joelkoz, 2022-05-08:
Thanks for checking out the project.  Build instructions are actually on the hackaday page here: https://hackaday.io/project/182645-qwickfab-pcb

Re: running from a PC instead of a pi - yes, you can. I've actually done that during development.  The system when first checked out of github assumes it will be set up on a Raspberry Pi with a Sharp LS055R1SX04 LCD with HDMI converted as screen #1, and a 480 x 320 SPI LCD touchscreen configured as display two. The Pi is configured in a multi-head mode which makes the display space look like on big canvas. Render images on the left side, and it appears on the Sharp LCD. Draw on the right side, and it appears on the SPI LCD.

The app is actually an Electron app, so the app window is just one large Chrome window that covers this entire screen area. This is important to know, because the UI and trace windows are layed out using HTML found in `app/render/index.html` and CSS found in `app/render/ui/ui.css` There are two primary `<div>` areas: one with an id of `mask-area` that contains a `<canvas>` with an id of `uv-mask` for the traces, and one with an id of `ui`.  The CSS positions these areas in such a way that `uv-mask` ends up displaying on the Sharp LCD, and the `ui` area is on the small display.  Assuming you know HTML and CSS, you can modify the CSS of `ui.css` to re-position the displays so the UI would appear on your PC screen, and the `uv-mask` would render on the LCD screen of the device you build.

nebulorum, 2022-05-08:
I did some digit into the Pi setup and kind of inferred there was a giant canvas. It also seems you can run separate screens. Not sure how to do the same on Mac, but I can investigate.

Is there a way to sale down the Display for testing (so I get the entire screen on  my viewport)? I find using the virtual buttons hard since most of the screen is out of my view port.

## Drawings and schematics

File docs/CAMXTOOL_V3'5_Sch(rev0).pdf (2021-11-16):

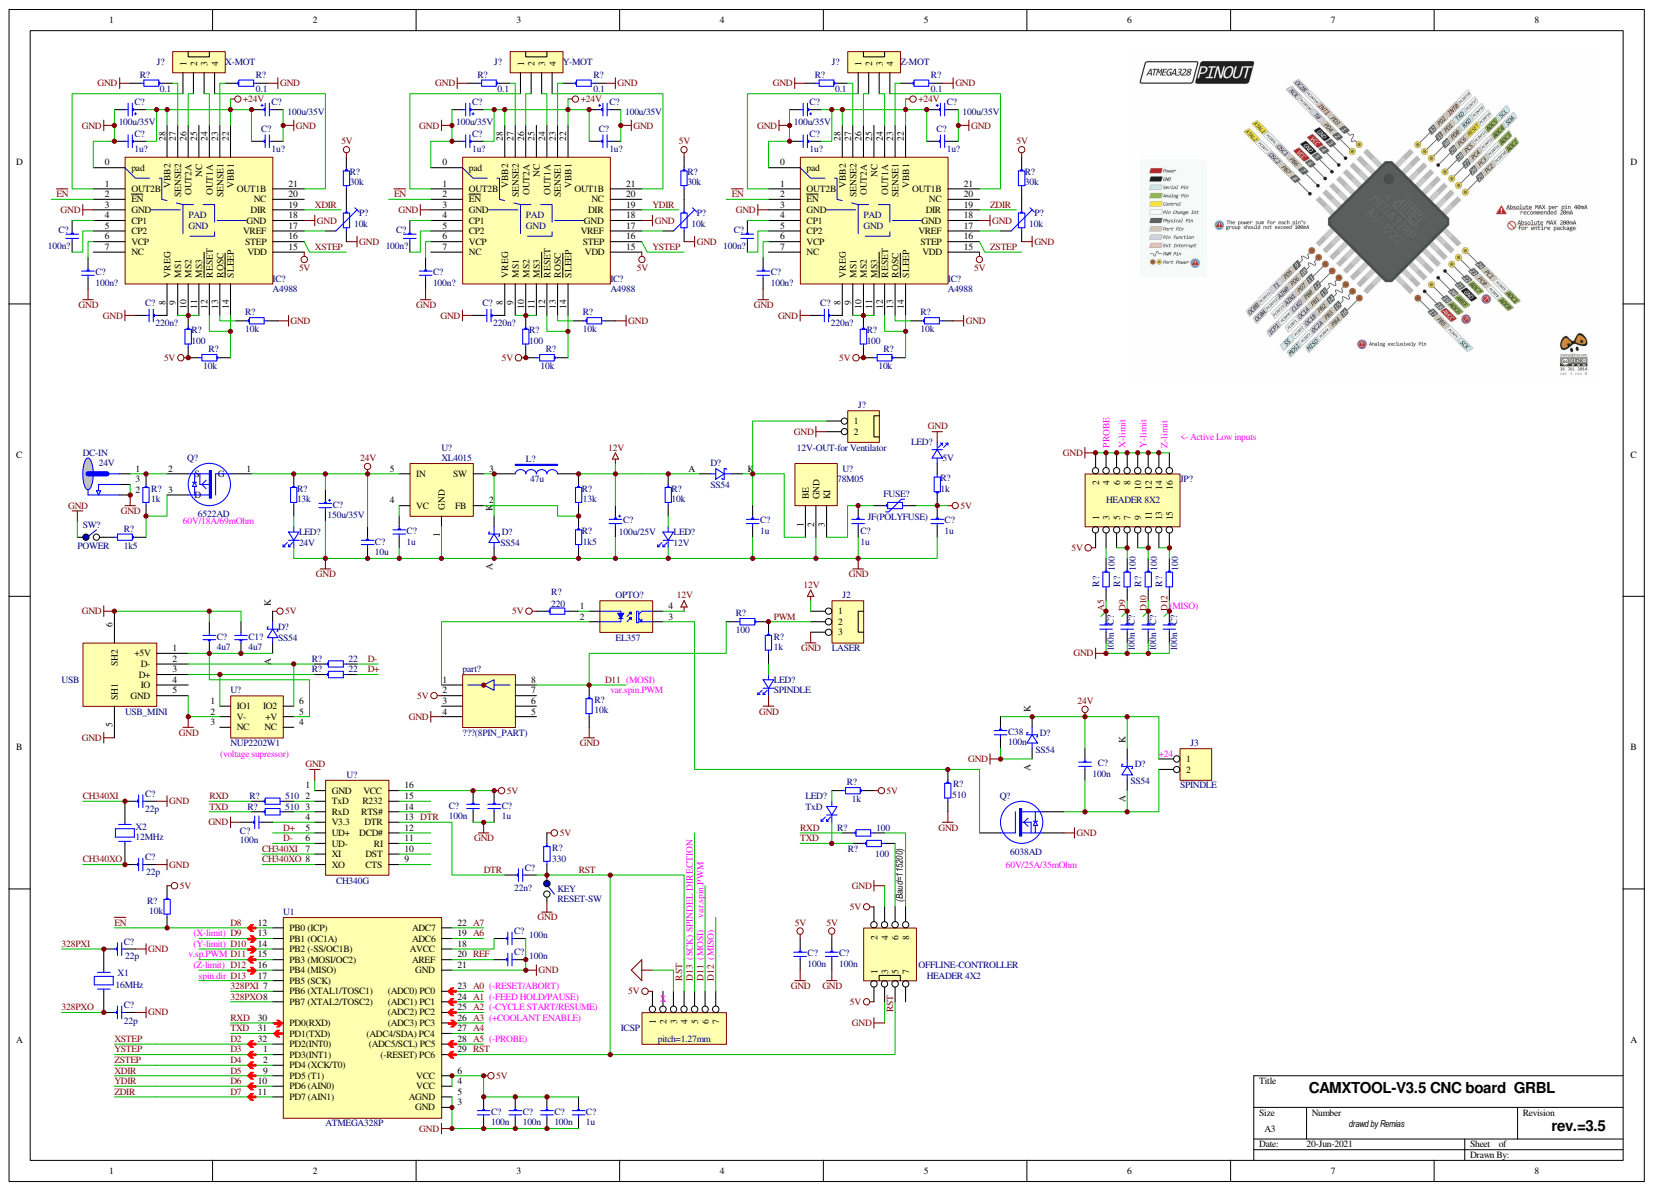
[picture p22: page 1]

CAMXTOOL-V3.5 CNC board GRBL

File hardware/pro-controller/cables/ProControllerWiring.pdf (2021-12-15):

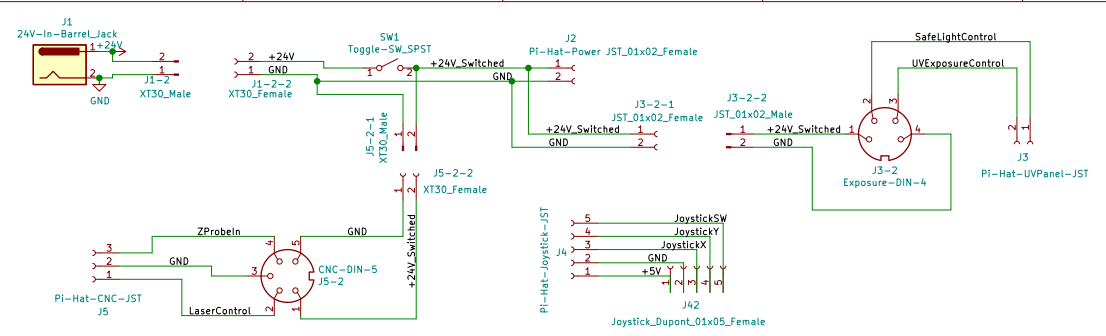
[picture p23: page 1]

J3 Pi-Hat-UVPanel-JST

J4 Pi-Hat-Joystick-JST

J5 Pi-Hat-CNC-JST

File: ProControllerWiring.sch Sheet: /
Id: 1/1 Title:

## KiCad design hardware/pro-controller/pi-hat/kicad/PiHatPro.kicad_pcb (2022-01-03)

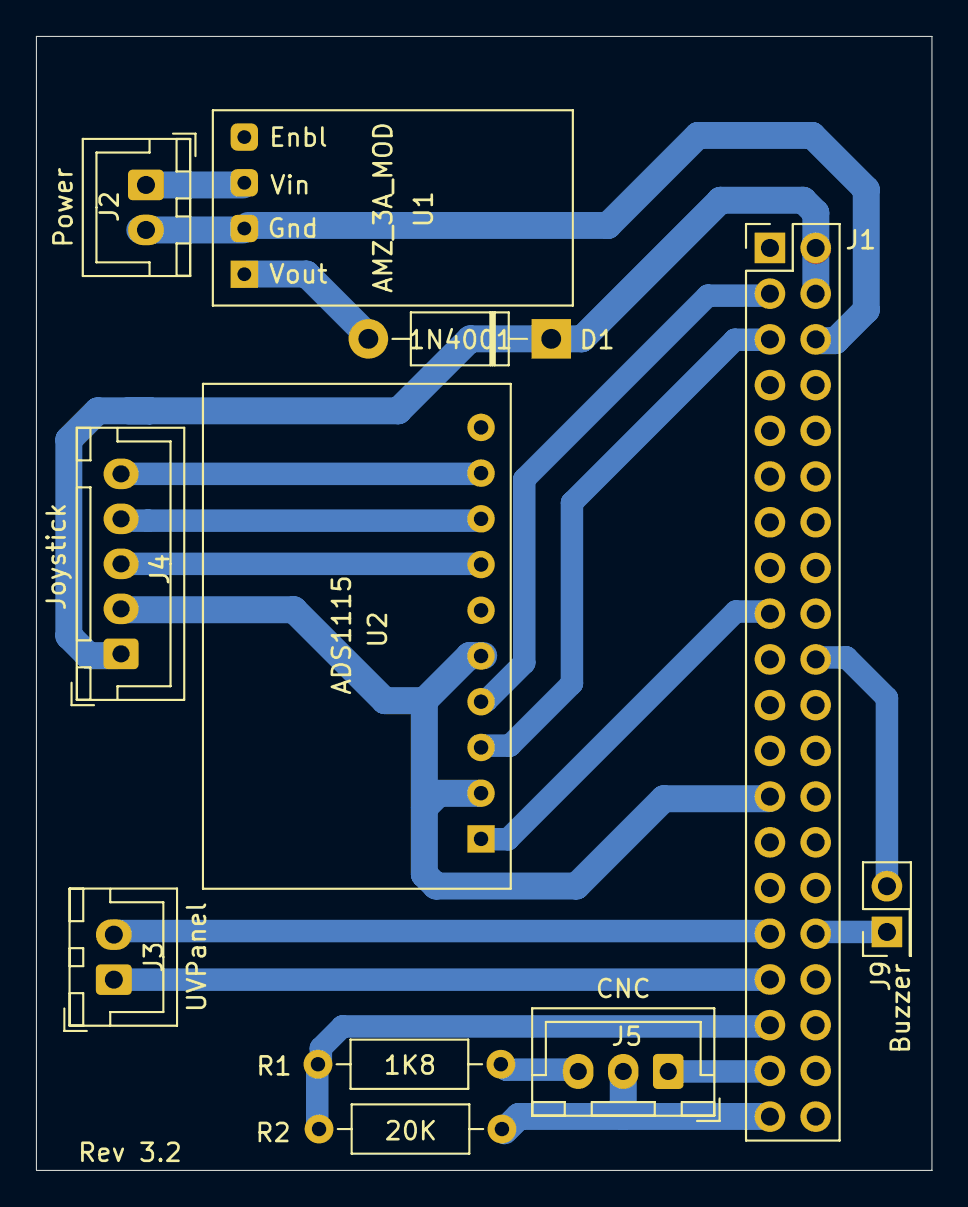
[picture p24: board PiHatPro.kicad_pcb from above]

Board: 4 copper layers, 49.8 x 63.0 mm, 11 parts (0 on the bottom side), 16 nets.

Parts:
D1: 1N4001; D_DO-41_SOD81_P10.16mm_Horizontal
J1: Raspberry_Pi_2_3; PinSocket_2x20_P2.54mm_BacksideMount
J2: Power; JST_XH_B2B-XH-A_1x02_P2.50mm_Vertical
J3: UVPanel; JST_XH_B2B-XH-A_1x02_P2.50mm_Vertical
J4: Joystick; JST_XH_B5B-XH-A_1x05_P2.50mm_Vertical
J5: CNC; JST_XH_B3B-XH-A_1x03_P2.50mm_Vertical
J9: Buzzer; PinHeader_2x01_P2.54mm_Vertical
R1: 1K8; R_Axial_DIN0207_L6.3mm_D2.5mm_P10.16mm_Horizontal
R2: 20K; R_Axial_DIN0207_L6.3mm_D2.5mm_P10.16mm_Horizontal
U1: AMZ_3A_MOD; Amazon_3A_Power_Module
U2: ADS1115; Adafruit_ADS1115_Module

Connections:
+3V3: J1.1, J1.17, U2.1
+5V: D1.1, J1.2, J1.4, J4.1
+24V: J2.1, U1.3
Buzzer: J1.32, J9.1
GND: J1.6, J1.9, J1.14, J1.20, J1.25, J1.30, J1.34, J1.39, J2.2, J4.2, J5.2, J9.2, R2.2, U1.2, U2.2, U2.5
JOYSTICK_SW: J4.5, U2.9
JOYSTICK_X: J4.3, U2.7
JOYSTICK_Y: J4.4, U2.8
LaserControl: J1.37, J5.1
unnamed: D1.2, U1.1
SCL: J1.5, U2.3
SDA: J1.3, U2.4
UVExpose: J1.31, J3.2
UVSafe: J1.33, J3.1
ZProbe3V3: J1.35, R1.2, R2.1
ZProbeIn: J5.3, R1.1

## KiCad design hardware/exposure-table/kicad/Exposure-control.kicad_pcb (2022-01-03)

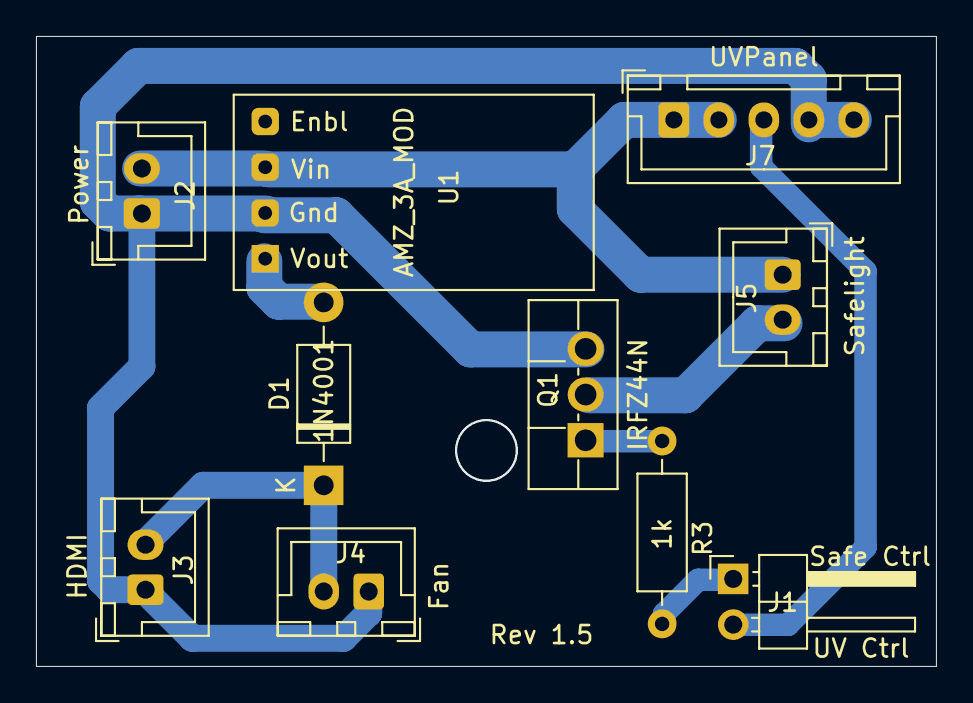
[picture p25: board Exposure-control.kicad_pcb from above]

Board: 2 copper layers, 50.0 x 35.0 mm, 10 parts (0 on the bottom side), 8 nets.

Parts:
D1: 1N4001; D_DO-41_SOD81_P10.16mm_Horizontal
J1: Light Control; PinHeader_1x02_P2.54mm_Horizontal
J2: Power; JST_XH_B2B-XH-A_1x02_P2.50mm_Vertical
J3: HDMI; JST_XH_B2B-XH-A_1x02_P2.50mm_Vertical
J4: Fan; JST_XH_B2B-XH-A_1x02_P2.50mm_Vertical
J5: Safelight; JST_XH_B2B-XH-A_1x02_P2.50mm_Vertical
J7: UVPanel; JST_XH_B5B-XH-A_1x05_P2.50mm_Vertical
Q1: IRFZ44N; TO-220F-3_Vertical
R3: 1k; R_Axial_DIN0207_L6.3mm_D2.5mm_P10.16mm_Horizontal
U1: AMZ_3A_MOD; Amazon_3A_Power_Module

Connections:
+5V: D1.1, J3.2, J4.2
+24V: J2.2, J5.1, J7.1, J7.2, U1.3
GND: J2.1, J3.1, J4.1, J7.4, J7.5, Q1.3, U1.2
unnamed: D1.2, U1.1
unnamed: Q1.1, R3.2
SafelightControl: J1.1, R3.1
SafelightGnd: J5.2, Q1.2
UVControl: J1.2, J7.3

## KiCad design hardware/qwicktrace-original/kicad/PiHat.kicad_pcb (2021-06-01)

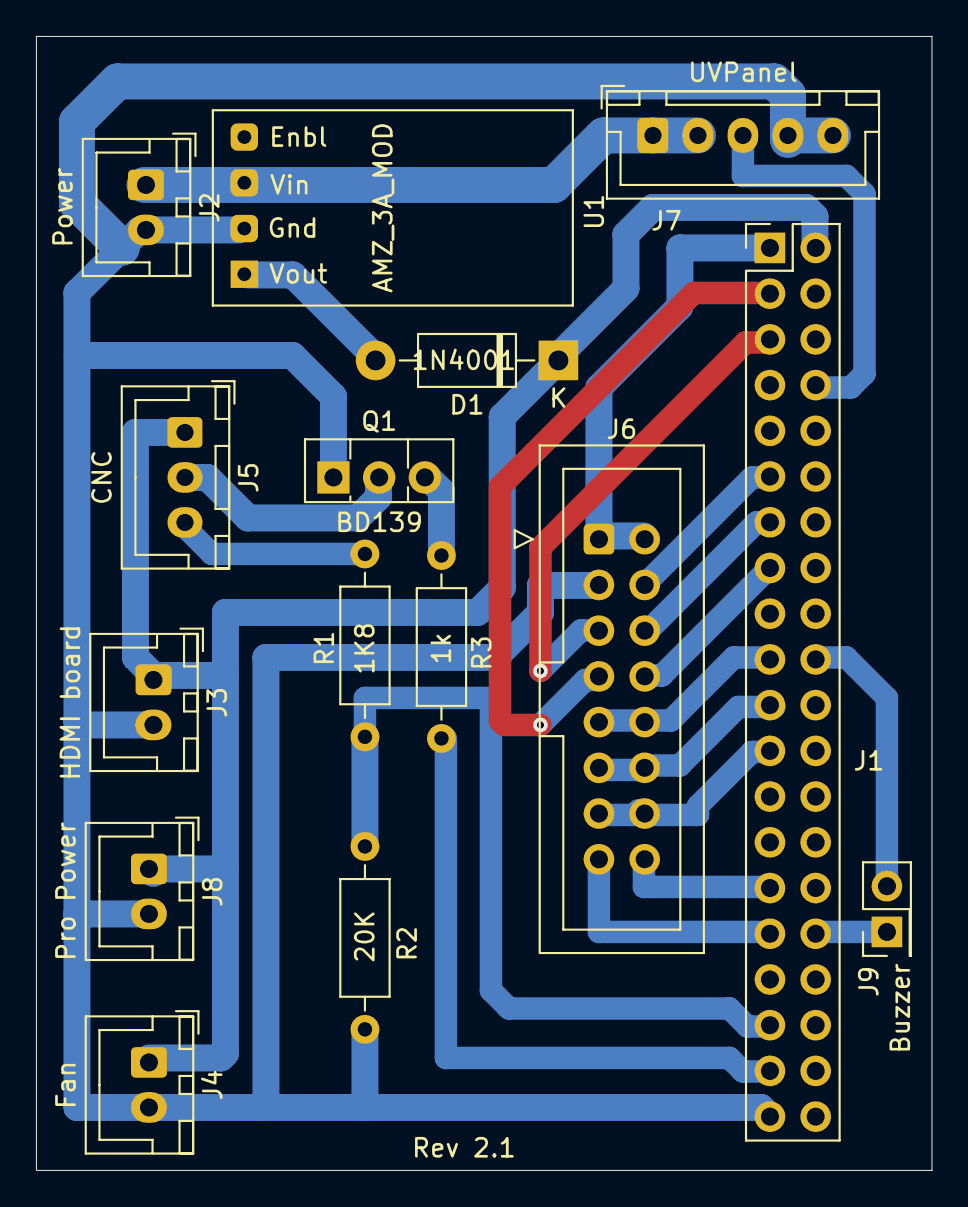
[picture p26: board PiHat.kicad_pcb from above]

Board: 2 copper layers, 49.8 x 63.0 mm, 15 parts (0 on the bottom side), 22 nets.

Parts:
D1: 1N4001; D_DO-41_SOD81_P10.16mm_Horizontal
J1: Raspberry_Pi_2_3; PinSocket_2x20_P2.54mm_BacksideMount
J2: Power; JST_XH_B2B-XH-A_1x02_P2.50mm_Vertical
J3: HDMI board; JST_XH_B2B-XH-A_1x02_P2.50mm_Vertical
J4: Fan; JST_XH_B2B-XH-A_1x02_P2.50mm_Vertical
J5: CNC; JST_XH_B3B-XH-A_1x03_P2.50mm_Vertical
J6: IDC16; IDC-Header_2x08_P2.54mm_Vertical
J7: UVPanel; JST_XH_B5B-XH-A_1x05_P2.50mm_Vertical
J8: Pro Power; JST_XH_B2B-XH-A_1x02_P2.50mm_Vertical
J9: Buzzer; PinHeader_2x01_P2.54mm_Vertical
Q1: BD139; TO-126-3_Vertical
R1: 1K8; R_Axial_DIN0207_L6.3mm_D2.5mm_P10.16mm_Horizontal
R2: 20K; R_Axial_DIN0207_L6.3mm_D2.5mm_P10.16mm_Horizontal
R3: 1k; R_Axial_DIN0207_L6.3mm_D2.5mm_P10.16mm_Horizontal
U1: AMZ_3A_MOD; Amazon_3A_Power_Module

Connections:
+3V3: J1.1, J6.1, J6.2
+5V: D1.1, J1.2, J3.1, J4.1, J5.1, J8.1
+24V: J2.1, J7.1, J7.2, U1.3
Buzzer: J1.32, J9.1
CS: J1.11, J6.4
DC: J1.13, J6.6
GND: J1.20, J1.39, J2.2, J3.2, J4.2, J6.3, J7.4, J7.5, J8.2, J9.2, Q1.1, R2.2, U1.2
LaserControl: J1.37, R3.1
LaserGnd: J5.2, Q1.2
MISO: J1.21, J6.11, J6.12
MOSI: J1.19, J6.9, J6.10
unnamed: D1.2, U1.1
unnamed: Q1.3, R3.2
RESET: J1.15, J6.8
SCL: J1.5, J6.5
SDA: J1.3, J6.7
SLCK: J1.23, J6.13, J6.14
T_CS: J1.31, J6.15
T_IRQ: J1.29, J6.16
UVControl: J1.8, J7.3
ZProbe3V3: J1.35, R1.2, R2.1
ZProbeIn: J5.3, R1.1

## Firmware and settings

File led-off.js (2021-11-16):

const pigpioClient = require('pigpio-client');
const pigpio = pigpioClient.pigpio({host: '127.0.0.1', port: '8888'});
// const pigpio = pigpioClient.pigpio({host: '192.168.0.152', port: '8888'});

const ready = new Promise((resolve, reject) => {
  console.log('Attempting to connect to pigpio...');
  pigpio.once('connected', resolve);
  pigpio.once('error', reject);
});

function wait(ms) {
  return new Promise(resolve => setTimeout(resolve, ms));
}

ready.then(async (info) => {
  // display information on pigpio and connection status
  console.log(JSON.stringify(info,null,2));
 
  const uv = pigpio.gpio(6);
  await uv.modeSet('output');
  console.log('UB Bed off');
  await uv.write(0);  // turn off
 
  // control Safelight
  const safelight = pigpio.gpio(13);
  await safelight.modeSet('output');
  console.log('Safelight off')
  await safelight.write(0);

  console.log('done');
  process.exit();
  
}).catch(() => (err) => {
  console.log(`Error: ${err}`)
});

console.log('done');

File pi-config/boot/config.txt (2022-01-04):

# For more options and information see
# http://rpf.io/configtxt
# Some settings may impact device functionality. See link above for details
# uncomment if you get no picture on HDMI for a default "safe" mode
#hdmi_safe=1
# uncomment this if your display has a black border of unused pixels visible
# and your display can output without overscan
#disable_overscan=1
# uncomment the following to adjust overscan. Use positive numbers if console
# goes off screen, and negative if there is too much border
#overscan_left=16
#overscan_right=16
#overscan_top=16
#overscan_bottom=16
# uncomment to force a console size. By default it will be display's size minus
# overscan.
#framebuffer_width=1280
#framebuffer_height=720
# uncomment if hdmi display is not detected and composite is being output
#
# uncomment to force a specific HDMI mode (this will force VGA)
#hdmi_group=1
#hdmi_mode=1
# uncomment to force a HDMI mode rather than DVI. This can make audio work in
# DMT (computer monitor) modes
#hdmi_drive=2
# uncomment to increase signal to HDMI, if you have interference, blanking, or
# no display
#config_hdmi_boost=4
# uncomment for composite PAL
#sdtv_mode=2
#uncomment to overclock the arm. 700 MHz is the default.
#arm_freq=800
# Uncomment some or all of these to enable the optional hardware interfaces
dtparam=i2c_arm=on
#dtparam=i2s=on
dtparam=spi=on
# Uncomment this to enable infrared communication.
#dtoverlay=gpio-ir,gpio_pin=17
#dtoverlay=gpio-ir-tx,gpio_pin=18
# Additional overlays and parameters are documented /boot/overlays/README
# Enable audio (loads snd_bcm2835)
dtparam=audio=off

# Disable Bluetooth
dtoverlay=disable-bt

[pi4]
# Enable DRM VC4 V3D driver on top of the dispmanx display stack
#dtoverlay=vc4-fkms-v3d
max_framebuffers=3

[all]
#dtoverlay=vc4-fkms-v3d

[HDMI:0]
## For Sharp LCD display------------
hdmi_ignore_edid=0xa5000080
hdmi_force_hotplug=1
hdmi_group=2
hdmi_mode=87
hdmi_drive=1
disable_overscan=1
framebuffer_width=1440
framebuffer_height=2560
max_framebuffer_width=1440
max_framebuffer_height=2560
hvs_priority=0x32ff
hdmi_pixel_freq_limit=400000000
hdmi_timings=1440 0 112 160 272 2560 0 4 4 3 0 0 0 48 0 244940000 3


[all]
## Framebuffers must match for X11 to run
framebuffer_depth=16


dtoverlay=uctronics-hslcd35

[HDMI:1]
gpu_mem=256
disable_overscan=1
hdmi_force_hotplug=1
hdmi_group=2
hdmi_mode=87
hdmi_cvt 480 320 60 6 0 0 0
hdmi_drive=2


[all]
## Default GPIO settings for Qwicktrace Pro LED and CNC laser pointer pins
gpio=6,26=op,dl
gpio=13=op,dh

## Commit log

2021-03-26 Added TFT wiring table. Print to PDF
    Updated Numbers spreadsheet. Printed to PDF for non Mac users.
2021-03-26 pi-config directory
    Moved 'overlays' to 'pi-config', then added additional configuration files.
    [config.txt]
2021-03-27 Update config.txt
    Comment out dtoverlay until after overlay file has been compiled.
    [config.txt]
2021-03-27 Correct LED control pin number in test code
    [led-off.js]
2021-03-28 Added pi-hat directory
    Various files for creating the PiHat needed to interface Raspberry Pi with hardware
    [PiHat.kicad_pcb, PiHat.sch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]
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2021-03-29 Improved Gerber files for 3rd party fab
    [PiHat.kicad_pcb, PiHat.sch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]
2021-03-29 Script to bundle files for easypcbusa.com
    Script creates a .zip file compatible with EasyPCBUSA.com for PCB fab
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2021-03-31 Re-arranged PiHat pins for TFT interface board
    First draft of small interface board to allow TFT screen to be connected with IDC or FFC connectors. To accommodate this, a few TFT pin assignments (Touch IRQ and Chip Select) were swapped.
    [PiHat.kicad_pcb, PiHat.sch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]
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2021-04-05 tighten display margins
2021-04-06 Render Gerber files with correct alignment
2021-05-20 Use Sparkmaker UV lamp on pin 14
    Move UV exposure control to pin 14. Pin 26 is now target (laser) pointer on/off for optional CNC machine.
2021-05-20 Updated pi hat schematics for rev2
    [PiHat-B_Cu.gbr, PiHat-B_Mask.gbr, PiHat-B_SilkS.gbr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]
2021-05-20 Added PCB for optional "Pro Controller"
    Pro Controller can work with QwickMill PCB CNC machine
    [ProController.kicad_pcb, ProController.sch]
2021-05-20 Removed TFT KiCad schematics
    Daughterboard for small TFT screen not used
    [TFT-B_Cu.gbr, TFT-B_Mask.gbr, TFT-B_SilkS.gbr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]
2021-05-20 Update PiHat.kicad_pcb
    Change default layer selections and file rendering
    [PiHat.kicad_pcb]
2021-05-20 Update PiHat-B_Cu.gbr
    Rev 2 of PiHat
    [PiHat-B_Cu.gbr]
2021-05-22 PiHat Rev 2.1
    Fix UV lamp ground thru GPIOs. Added buzzer trace.
    [PiHat-B_Cu.gbr, PiHat-B_Mask.gbr, PiHat-B_SilkS.gbr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]
2021-05-22 Moved some txt to front silk screen layer of Rev2.1 PiHat
    [PiHat-B_Cu.gbr, PiHat-B_Mask.gbr, PiHat-B_SilkS.gbr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]
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2021-05-28 Tweaks to cnc-joystick-test
    Remove old code. Control laser via key press. Ability to zero work coordinates
2021-06-01 Updated PiHat schematic to reflect proper values to read z-probe
    [PiHat.kicad_pcb, PiHat.sch]
2021-06-01 Fixed sporadic joystick button detection
    [joystick-test.js]
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2021-06-02 Spindle speed control added to CNC class
    rpm is now a settable property
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2021-06-22 Selection list now has optional list filter function
    [PiHat.drl]
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2021-06-23 WIP: Select deskew alignment holes
    Initial code for deskew location selection (simulate with mouse clicks for now).
2021-06-24 Drill alignment page uses transforms
    Use canvas transformation matrix to orient and scale hole positions
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2021-06-26 WIP: Deskew and drill board using CNC
    Fixes and additions to cnc drilling code. Use transformation matrix to convert to/from pcb coordinates and mill coordinates.
2021-06-26 Update QwickMill-init.nc
    Change mill orientation to X+ is right, Y+ is up, origin is normally upper right.
2021-06-27 Corrected pin definitions in standard Pi-Hat
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2021-06-30 Refactor UI to be "project based" vs. individual file based
    Refactor file loading code to use a PCBProject defined ideally as a gbrjob file (bot not required). Also includes preliminary code for milling PCBs as well as exposing them.
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2021-07-15 Code fixes to allow remote testing of GPIO interfaces
    [cnc-joystick-test.js]
2021-07-16 Correct joystick jog direction
    [cnc-joystick-test.js]
2021-07-16 FIX: joystick i2c uses pigpio i2c code
    Allow complete remote operation by supporting i2c via pigpio vs. i2c-bus
    [cnc-joystick-test.js]
2021-07-16 Fixes to wizard subsystem
    Wizard buttons had wrong css class. cancelWizard() now fault tolerant
2021-07-16 Fix display of conditional buttons
    Certain buttons are available if certain conditions are met. This fixes the code that makes that happen
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2021-07-16 Fixes from testing
    Fixes for bugs found during mill wizard testing
2021-07-17 Add "Reset mill" option to settings
2021-07-17 Fixes to CNCController
    Debounce joystick button, popup messages on error events, initCNC() should reset sender and feeder also, add a timeout to waitForState()
2021-07-18 Fixes to mill setup
    Use proper coordinate system when commanding machine during setup.
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2021-07-19 Fixes to gcode loading and autoleveling pre-mill
    Testing of pcb milling gcode loading and autoleveling
2021-07-21 Add margin parameter to GerberUtils rotate
    Initial code to fix rotation adjustments when edge cuts are unknown.
2021-07-21 Add BoundingBox class for use by GerberData
    GerberData now tracks bounding boxes for the indiv idual files. Initial code to fix rotation adjustments when edge cuts are unknown.
2021-07-21 Lazy load and save GerberData as part of PCBProject
    PCBProject object now loads and tracks its own instance of GerberData for all of the files in the project. This gives access to bounding boxes and drill holes. Part of initial code to fix rotation adjustments when edge cuts are unknown.
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2021-07-25 Fixed missing property reference
    GerberData refactor changed definition of boundingBox property
    [Test.kicad_pcb, Test.sch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]
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2021-07-25 Rewrite mirror routines using transformation matrixes
    [after.drl, after.gbr]
2021-07-26 Fix simulated corners bounding box when no edge file is missing
    Wrong property was used in calculation
    [after.drl, after.gbr, longx-B_Cu.gbr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]
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2021-07-26 Fixed Z search speed on PCB z probe
2021-07-26 Do not use pcb2gcode tool change gcode
    pcb2gcode generates tool change code. Remove that at runtime, as the mill is already prepped.
    [Test.kicad_pcb, Test.sch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]
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2021-09-07 Remove pcbFrame references
    The PCB frame is no longer used in the design
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2021-09-09 Finish IPC Refactor and Testing
    Refactor the legacy code to use the new ipc MQ system. Test the milling process, and fix any errors introduced by recent refactors.
2021-09-09 Small fixes to actual milling process
2021-09-11 Corrected stock handling code
    Can now properly detect if currently loaded and processed stock can be used in the next operation
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2021-09-30 Initial fixes to Drill Alignment process
    Fixes to the "align drill holes" process. Includes major fixes to GerberCanvas to properly display traces and drill holes in the UI, as well as tweaks to the other code to support the Drill action.
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2021-09-30 Fixes from drill testing
    Corrections to the alignment and drilling processes
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2021-10-08 Latest config.txt for Pro controller using UCTRONICS UC640
    [config.txt]
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2021-10-15 Custom stock entry, plus positioning fixes
    Added ability to specify a custom stock size. Also make fixes to the "board positioning" code found during testing.
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2021-10-23 Fix "Cancel" function of PCB vertical cut
2021-10-23 Removed temp files from test dir
    [Test.kicad_pcb, Test.sch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]
2021-10-23 Reorganize PCB design directories
    Re-arrange PCB design files
    [Exposure-controll.kicad_pcb, Exposure-controll.sch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]
2021-10-23 FIX: UIController wrong identifier used for current profile
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2021-10-25 Fixes to drilling process
    First (quasi) successful drill following mill. Includes moving board positioning to the "prepare for work" phase of the ProjectLoader
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2021-10-25 Fixes to exposure control board
    [Exposure-control.kicad_pcb, Exposure-control.sch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]
2021-10-25 Remove files from pcb-files directory
    [PiHat-B_Cu.gbr, PiHat.drl]
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2021-10-25 Joystick i2c fault tolerance
    Ignore transient errors on ADS1115 joystick interface
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2021-10-25 FIX: Incorrect ZHeight at beginning of milling
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2021-10-26 Fix: drilling after milling needs actual stock used in profile
    Drill holes were off immediately following mill due to "actual" property from last profile not in new profile stock property.
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2021-10-26 Fixed milling progress display
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2021-10-28 Exposure control board rev 1.5
    Moved signal connectors to opposite side. Added screw hole to connect to exposure table body
    [Exposure-control.kicad_pcb]
2021-10-28 Drilling PCB zprobes PCB and not zProbe pad
    Too much variability discovered in ZPad probe to PCB offset
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2021-10-28 Tweaks to pcb mill settings
    traces needed to be a little bit deeper - otherwise, missed areas.
2021-10-28 FIX: multi-monitor config w/ U640
    Update the multi-monitor x-config to use fb2 (the frame buffer used by U640)
2021-11-02 FIX: changing board position fails on same project
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2021-11-06 Fixes to mask calibration process
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2021-11-10 FIX: Vertical cut on spoil board alignment channels were off
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2021-11-11 Fixes to exposure mask display and calibration
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2021-11-12 STL files
    Added STL files needed for 3D printed parts
    [AlignmentFrame.stl, BaseBack.stl, BaseFront.stl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]
2021-11-13 Initial etch tank STL and instructions
    [Base.stl]
2021-11-16 Added STL file for etch tank
    [Base.stl, Basket.stl, ControlLid.stl]
2021-11-16 Disable bluetooth in config
    [config.txt]
2021-11-16 Update joystick-test-raw.js
    Fixed i2c bus number
    [joystick-test-raw.js]
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2021-11-22 Initial "project upload" code
    PCB projects are now in individual directories. A small web page allows the .zip files of the entire project to be uploaded to the device.
    [Test-Edge_Cuts.gbr]
2021-12-15 Added schematics for ProController wiring
    [ProControllerWiring.kicad_pcb, ProControllerWiring.sch]
2021-12-15 Move Kicad files to hardware subdir
    [Exposure-control.kicad_pcb, Exposure-control.sch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]
2021-12-15 Move STL files to hardware directory
    [AlignmentFrame.stl, Base.stl, BaseBack.stl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]
2021-12-15 Moved original KiCad files to hardware dir
    [PiHat.kicad_pcb, PiHat.sch]
2021-12-17 Pi Hat is now single sided
    Pi Hat Rev 3.1 is now completely single sided for easier DIY fabrication
    [PiHatPro-B_Cu.gbr, PiHatPro-B_Mask.gbr, PiHatPro-B_SilkS.gbr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]
2022-01-03 Updated exposure control board
    Changed to power MOSFET to control safelight
    [Exposure-control.kicad_pcb, Exposure-control.sch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]
2022-01-03 Fixes to PiHatPro pcb board
    [PiHatPro-B_Cu.gbr, PiHatPro-B_Mask.gbr, PiHatPro-B_SilkS.gbr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]
2022-01-03 JCLPCB compatible gerber files
    [PiHatPro-B_Cu.gbr, PiHatPro-B_Mask.gbr, PiHatPro-B_Paste.gbr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]
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2022-01-03 Fixed silk-screen on PiHat board
    Certain silked values were overlapping holes.
    [PiHatPro-B_Cu.gbr, PiHatPro-B_Mask.gbr, PiHatPro-B_Paste.gbr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]
2022-01-04 Safelight on for boot
    Turn the safelight on while booting so user can watch screen initialization.
    [config.txt]
2022-01-05 FIX: edge cut files not processed correctly
    Fix processing of edge cut files in .zip upload
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2022-01-06 Fix alignment issue bottom board
    trace position for bottom side needs to be corrected if stock height does not match original board height and vertical position is not being altered via "GerberTransform.positionCopper()"
2022-01-06 Fix side mirroring for exposures
    When doing exposures, the mask mirroring is the opposite of when doing milling
2022-02-25 Fix rotated copper positions in GerberTransforms
    Rotating copper the moving right had wrong positioning
2022-02-25 Fix prepareForWork() transformations
    When preparing for work, the project loader did not create properly transformed gerber and drill files.
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2022-02-25 FIX: Exposing needs to mirror bottom also
    Bottom side is mirrored if milling or exposing
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2022-06-08 Skip ZPad position finding during zprobe
    ZPad probe serves no useful purpose at the moment, so skip it.
2022-06-08 Skip zpad calculations when probing for pcb surface
    ZPad no longer used for pcb surface probe
2022-06-08 FIX: Initial loading of gbr project fails
    boundingBoxes property of PCBProject was not properly set upon initial upload of project .zip file
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2025-04-12 FIX: DRL files output by Eagle are missing final EOL
    The lack of EOL on output of DRL files causes problems with gerber parsing code
